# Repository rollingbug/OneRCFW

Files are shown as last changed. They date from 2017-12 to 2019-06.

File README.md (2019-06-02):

# OneRCFW
An Arduino/AVR based flight controller for RC fixed wing.  

    - 5 input channels (Throttle, Ailerons, Elevator, Rudder, flight mode)  
    - 4 output channels (0.5 us resolution PWM/PPM signal generator).  
    - Airplane NED attitude tracking function (with 6 DOF sensor, 200 Hz attitude update rate).
    - Airplane auto level (roll and pitch) control function.  
    - Airplane heading lock control function.  
    - Airplane flight mode control function (manual mode, auto level mode and GPS mode).  
    - Airplane GPS return to home function (unstabled, still need to do more test!)
    - RC output mixer function (for normal airplane, delta wing and V tail).  
    - 6 DOF sensor calibration function.  
    - Radio control stick position calibration function.    
    - Airplane failsafe function.  
    - Airplane configuration save/reload/reset function.  
    - Airplane runtime status monitoring function.  

PCB picture  

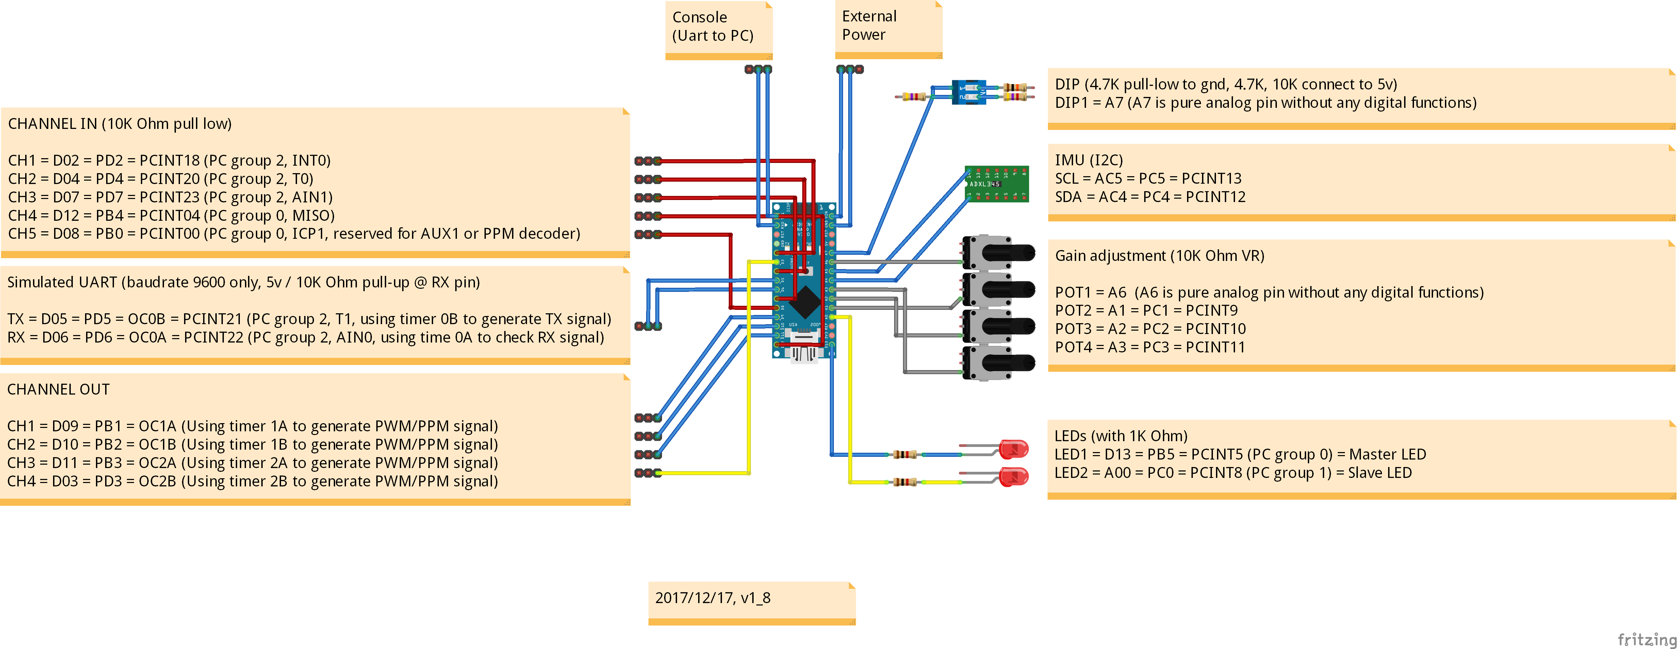
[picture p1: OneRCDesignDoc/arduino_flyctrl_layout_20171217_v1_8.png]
Pin assignment picture


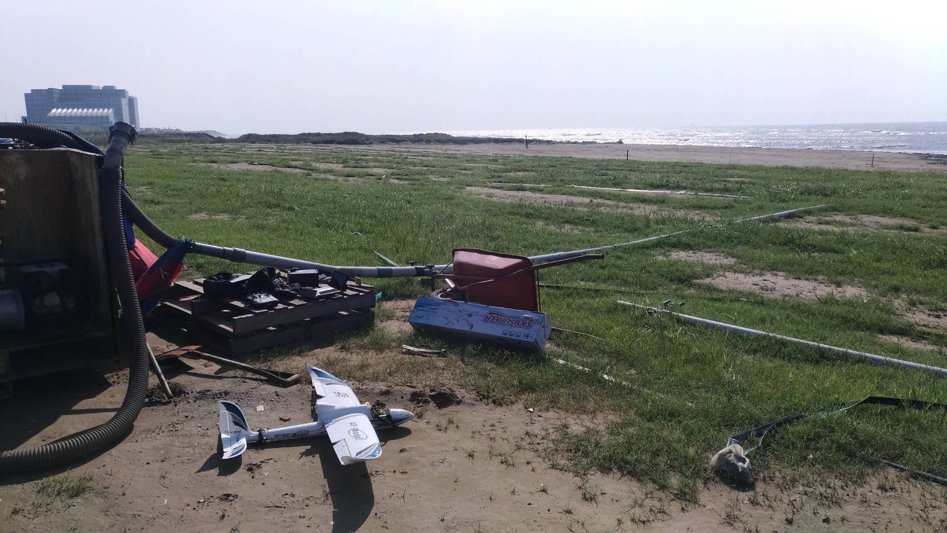
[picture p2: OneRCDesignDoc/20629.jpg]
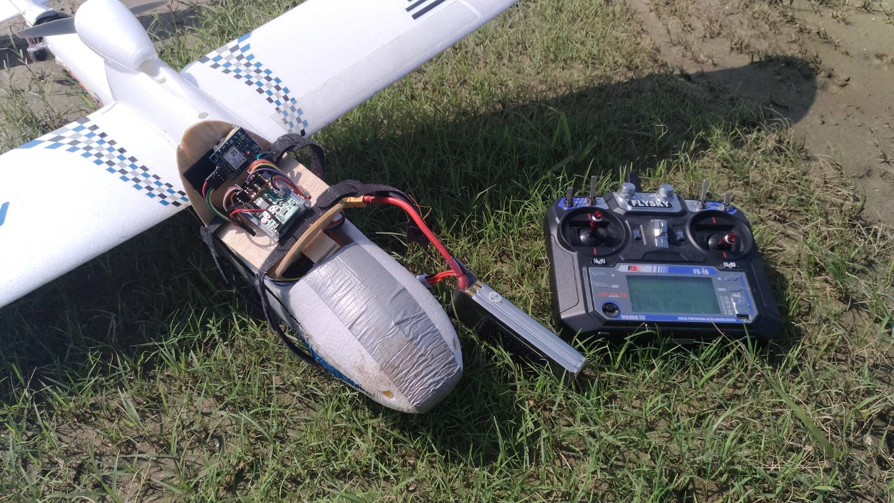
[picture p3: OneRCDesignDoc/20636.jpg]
  <br/><br/><br/>

Details:
---------------------
Flight controller source code: [OneRCFW](https://github.com/rollingbug/OneRCFW/tree/master/OneRCFW)  
Flight controller schematic and PCB layout: [OneRCSchematic_v1](https://github.com/rollingbug/OneRCFW/tree/master/OneRCSchematic/OneRCSchematic_v1)  
Flight controller test video: [20171029 FC test in very windy (12.5m/s) day.](https://www.youtube.com/watch?v=OjTpQ1Ft-OE)  
GUI monitoring tool: [OneRCGUI](https://github.com/rollingbug/OneRCFW/tree/master/OneRCGUI)  
Design documents: [OneRCDesignDoc](https://github.com/rollingbug/OneRCFW/tree/master/OneRCDesignDoc)   

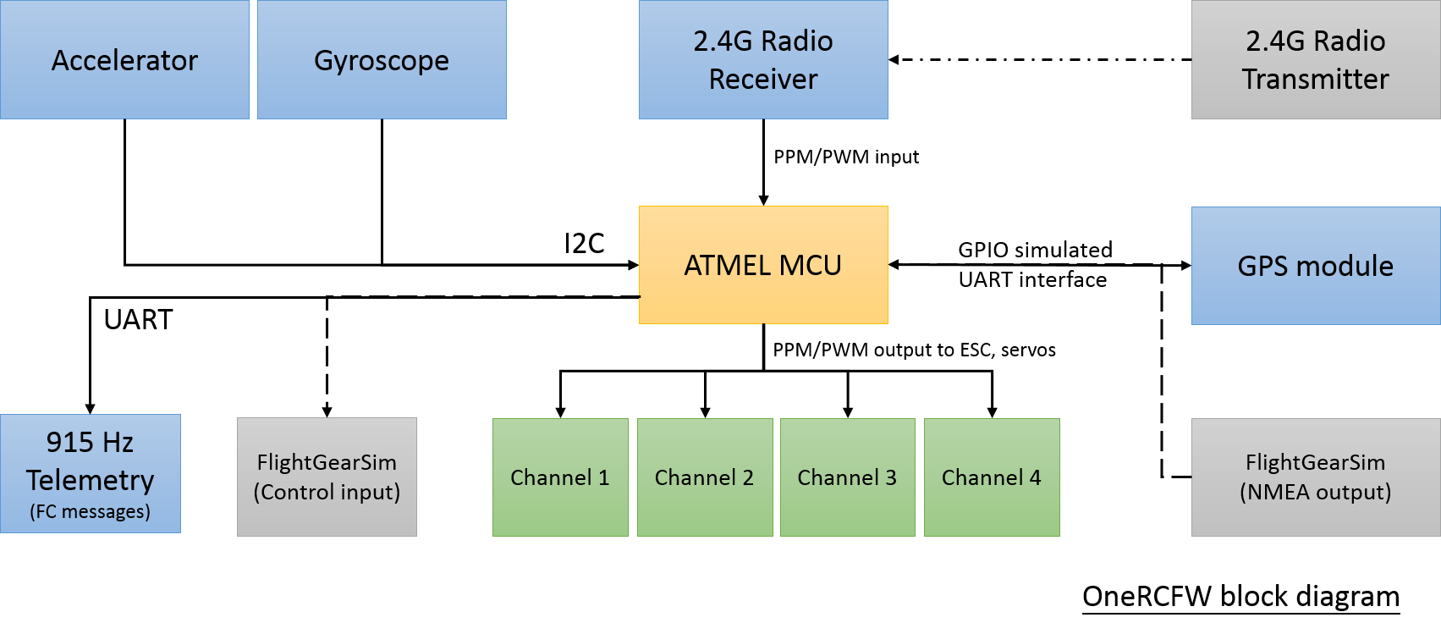
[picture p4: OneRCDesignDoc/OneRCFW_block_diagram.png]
FC block diagram


Build and Installation:
---------------------
1. Prepare Arduino 1.6.9 IDE.
2. Click the **OneRCAirplane.ino** to launch Arduino IDE. 
3. Change board type setting to "Arduino Nano" or "Pro Mini" and correct UART port setting.
4. Build and upload the firmware to Arduino or customized PCB.
5. Connect the Radio receiver to flight controller.
6. Check the channel output signal and the status of on board LEDs.<br/><br/><br/>

For Simulation mode:
---------------------
1. Download and instll FlightGear, and copy the protocol and configuration file to speicfic folder.
    - Copy [MAVLink.xml](https://github.com/rollingbug/OneRCFW/tree/master/OneRCFlightGearConf/MAVLink.xml) to FlightGear\data\Protocol\
    - Copy [.fgfsrc](https://github.com/rollingbug/OneRCFW/tree/master/OneRCFlightGearConf/.fgfsrc) to C:\Documents and Settings\{User name}\
2. Modify the #define IMU_SENSOR_MPU6050 in imu_ctrl.h, change to #define IMU_SENSOR_FG_SIM.
3. Rebuild and upload the firmware to Arduino.
4. Modify the COM port setting in both the [MP_fdm_nmea.py](https://github.com/rollingbug/OneRCFW/tree/master/OneRCGUI/MP_fdm_nmea.py) and [MP_fdm_sim.py](https://github.com/rollingbug/OneRCFW/tree/master/OneRCGUI/MP_fdm_sim.py), and lanuch these 2 files.
5. Lanuch fgfs.exe and enjoy the flight in simulator.

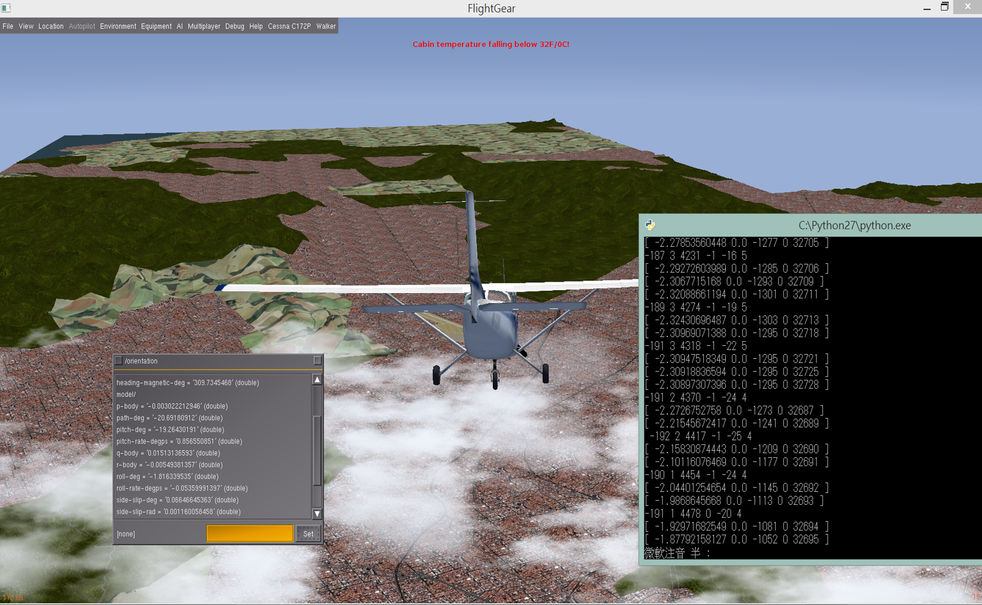
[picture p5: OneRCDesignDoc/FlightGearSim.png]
OneRC_FG_Simulator


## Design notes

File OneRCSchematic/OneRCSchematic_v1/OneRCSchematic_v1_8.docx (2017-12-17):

2017/08/19, v1.8

Part | Value | Package | Description | MF | MPN | BOM
C1 | 10uF | EIA3216 | CAP-00811 | AVX | TAJA106K010RNJ (10V, 10%) | 001
C2 | 10uF | EIA3216 | CAP-00811 | AVX | TAJA106K010RNJ (10V, 10%) | 001
C3 | 10nF (0402) | 0402-CAP | Capacitor | MuRata | GRM155R71H103KA88D (50v, X7R 10%) | 002
C4 | 1.0uF (0402) | 0402-CAP | Capacitor | YAGEO | CC0402KRX5R5BB105 (6.3v) | 003
C5 | 1.0uF (0402) | 0402-CAP | Capacitor | YAGEO | CC0402KRX5R5BB105 (6.3v) | 003
C6 | 0.1uF (0402) | 0402-CAP | Capacitor | MuRata | GRM155R71H104KE14D(50v, X7R 10%) | 004
C7 | 0.1uF (0402) | 0402-CAP | Capacitor | MuRata | GRM155R71H104KE14D(50v, X7R 10%) | 004
C8 | 0.1uF (0402) | 0402-CAP | Capacitor | MuRata | GRM155R71H104KE14D(50v, X7R 10%) | 004
C9 | 0.1uF (0402) | 0402-CAP | Capacitor | MuRata | GRM155R71H104KE14D(50v, X7R 10%) | 004
C10 | 10nF (0402) | 0402-CAP | Capacitor | MuRata | GRM155R71H103KA88D (50v, X7R 10%) | 002
C11 | 2.2nF (0402) | 0402-CAP | Capacitor | YAGEO | CC0402KRX7R9BB222, 2.2nF50V±10% | 005
C12 | 0.1uF (0402) | 0402-CAP | Capacitor | MuRata | GRM155R71H104KE14D(50v, X7R 10%) | 004
D1 | WHITE | 0402-LED | | CHIPLED | GTG1005SYGC | 200
D2 | RED | LED-0603 | Assorted Red LEDs | CHIPLED | GTG1608SURC | 201
D3 | BLUE | LED-0603 | Blue LEDs for production use | CHIPLED | GTG1608UBC | 202
J1 | BAT | 1X03 | Header 3 | UNKNOWN | UNKNOWN | 800
J2 | IN1 | 1X03 | Header 3 | UNKNOWN | UNKNOWN | 800
J3 | IN2 | 1X03 | Header 3 | UNKNOWN | UNKNOWN | 800
J4 | IN3 | 1X03 | Header 3 | UNKNOWN | UNKNOWN | 800
J5 | IN4 | 1X03 | Header 3 | UNKNOWN | UNKNOWN | 800
J6 | IN5 | 1X03 | Header 3 | UNKNOWN | UNKNOWN | 800
J7 | OUT1 | 1X03 | Header 3 | UNKNOWN | UNKNOWN | 800
J8 | OUT2 | 1X03 | Header 3 | UNKNOWN | UNKNOWN | 800
J9 | OUT3 | 1X03 | Header 3 | UNKNOWN | UNKNOWN | 800
J10 | OUT4 | 1X03 | Header 3 | UNKNOWN | UNKNOWN | 800
PH1 | PH1X3-05 | PH005-1-3 | | UNKNOWN | UNKNOWN | 801
PH2 | PH1X7-05 | PH005-1-7 | | UNKNOWN | UNKNOWN | 801
PH3 | PH1X4-05 | PH005-1-4 | | UNKNOWN | UNKNOWN | 801
R1 | 10K (0402) | 0402-RES | Resistor | YAGEO | RC0402FR-0710K | 100
R2 | 10K (0402) | 0402-RES | Resistor | YAGEO | RC0402FR-0710K | 100
R3 | 10K (0402) | 0402-RES | Resistor | YAGEO | RC0402FR-0710K | 100
R4 | 10K (0402) | 0402-RES | Resistor | YAGEO | RC0402FR-0710K | 100
R5 | 10K (0402) | 0402-RES | Resistor | YAGEO | RC0402FR-0710K | 100
R6 | 1K (0402) | 0402-RES | Resistor | YAGEO | RC0402FR-071K | 100
R7 | 10K (0402) | 0402-RES | Resistor | YAGEO | RC0402FR-0710K | 100
R8 | POT1 | RTRIM3202 | Trimm resistor | Panasonic | EVM3ESX50B14 | 101
R9 | POT2 | RTRIM3202 | Trimm resistor | Panasonic | EVM3ESX50B14 | 101
R10 | POT3 | RTRIM3202 | Trimm resistor | Panasonic | EVM3ESX50B14 | 101
R11 | 10K (0402) | 0402-RES | Resistor | YAGEO | RC0402FR-0710K | 100
R12 | POT4 | RTRIM3202 | Trimm resistor | Panasonic | EVM3ESX50B14 | 101
R13 | 4K7 (0402) | 0402-RES | Resistor | YAGEO | RC0402FR-074K7 | 102
R14 | 1K (0402) | 0402-RES | Resistor | YAGEO | RC0402FR-071K | 103
R15 | 4K7 (0402) | 0402-RES | Resistor | YAGEO | RC0402FR-074K7 | 102
R16 | 1K (0402) | 0402-RES | Resistor | YAGEO | RC0402FR-071K | 103
R17 | 10K (0402) | 0402-RES | Resistor | YAGEO | RC0402FR-0710K | 100
R18 | 10K (0402) | 0402-RES | Resistor | YAGEO | RC0402FR-0710K | 100
R19 | 10K (0402) | 0402-RES | Resistor | YAGEO | RC0402FR-0710K | 100
R20 | 10K (0402) | 0402-RES | Resistor | YAGEO | RC0402FR-0710K | 100
R21 | 10K (0402) | 0402-RES | Resistor | YAGEO | RC0402FR-0710K | 100
R22 | 10K (0402) | 0402-RES | Resistor | YAGEO | RC0402FR-0710K | 100
R23 | 10K (0402) | 0402-RES | Resistor | YAGEO | RC0402FR-0710K | 100
SW1 | SW1 | DIPSWITCH-02-50MIL | DIP SWITCH | Kingtek | DSHP02TSGET (1.27mm, 2P) | 700
T1 | 2N7002PW | SOT323 | N-channel TrenchMOS FET | ROHM | 2SK3018T106 | 903
T2 | 2N7002PW | SOT323 | N-channel TrenchMOS FET | ROHM | 2SK3018T106 | 903
U1 | RT9167 | SOT23-5 | MIC5205 150mA vreg | Richteck | RT9167A-33PB (3.3v, 500mA) | 900
U2 | MPU-6050 | QFN.24.4X4 | | InvenSense | MPU-6050 | 901
U3 | ATMEGA328P_TQFP | TQFP32-08 | | Atmel | ATMEGA328P_TQFP | 902
X1 | 53047-06 | 53047-06 | CONNECTOR | MOLEX | 53047-0610-C | 802
X2 | ICSP | PHB_1MM27_2X03_SNT | Pin Header Box-Type, 1.27mm/0.5/50mil Pitch | Connfly | DS1031-06-2*50P8BV等長 | 803
X3 | 53047-04 | 53047-04 | CONNECTOR | MOLEX | 53047-0410 | 804
Y1 | 16MHZ | RESONATOR-SMD | Resonator | MuRata | CSTCE16M0V53-R0 | 600

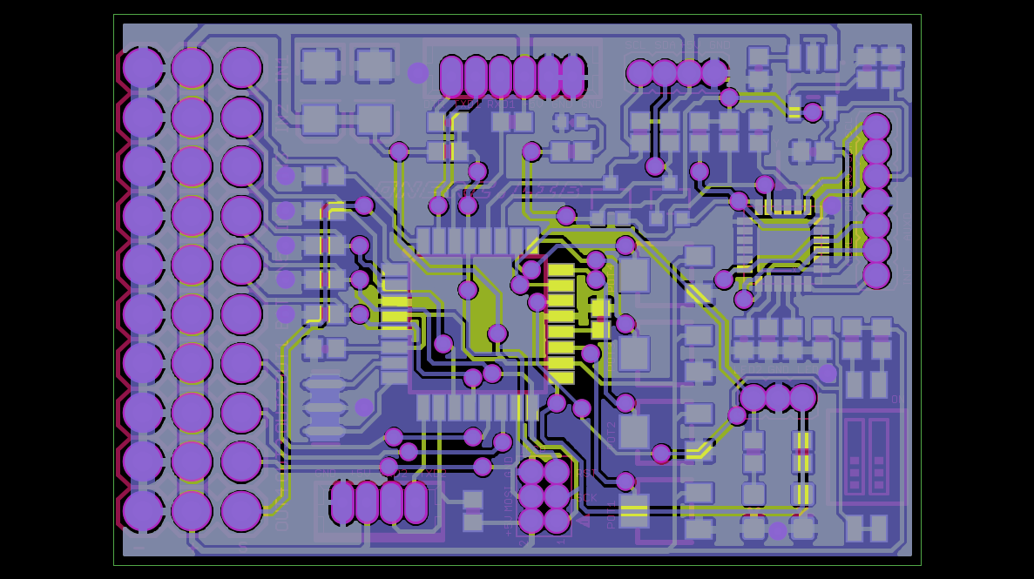
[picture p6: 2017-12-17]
OneRCSchematic/OneRCSchematic_v1/OneRCSchematic_v1_8.png

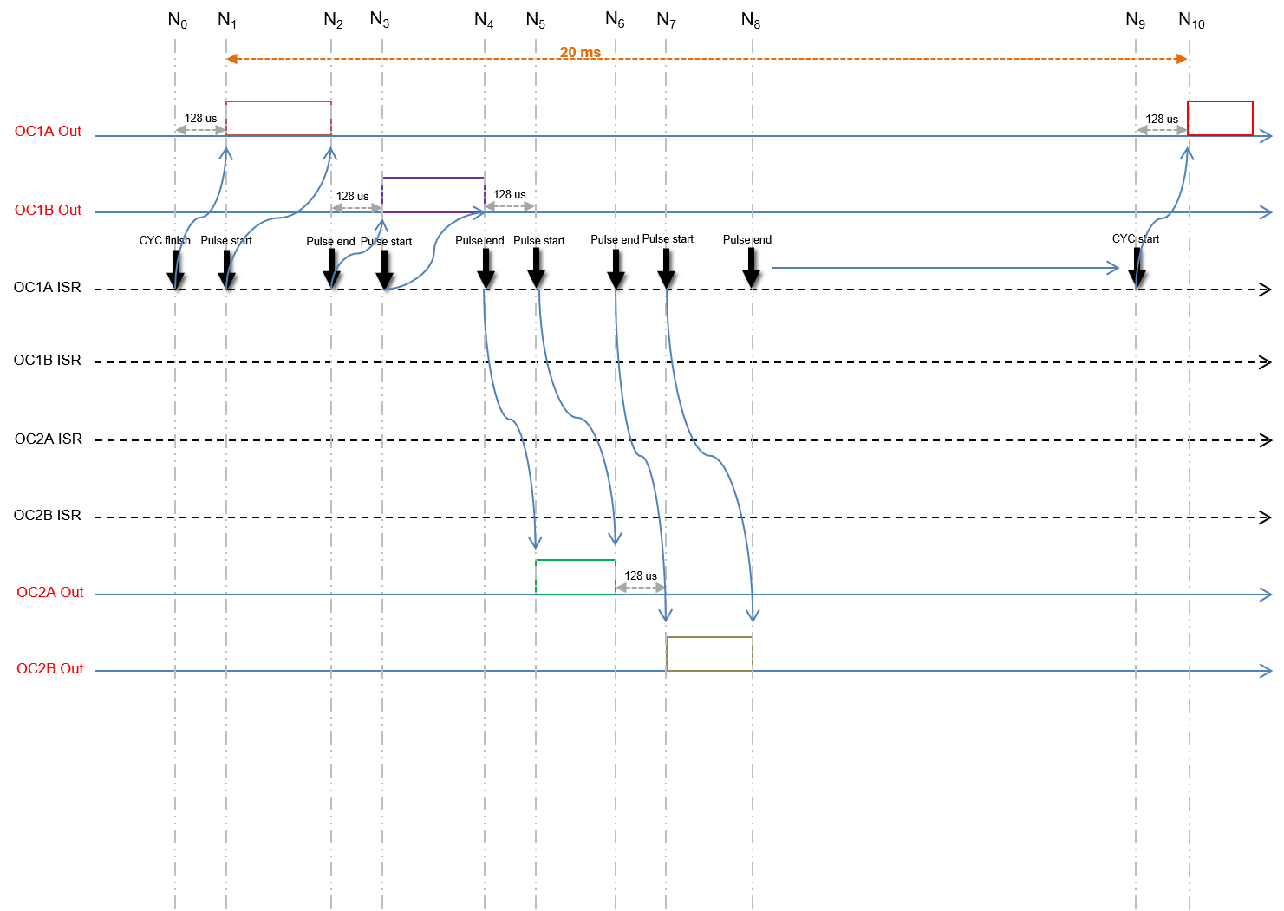
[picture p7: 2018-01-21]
OneRCDesignDoc/PWM_PPM_generator.png

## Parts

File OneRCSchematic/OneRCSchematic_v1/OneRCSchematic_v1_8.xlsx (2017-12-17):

Part | Value | Device | Package | Description | MF | MPN | BOM | NOTE | Ready | Price | OC_FARNELL | OC_NEWARK | PROD_ID | VALUE
C1 | 10uF | 10UF-16V-10%(TANT) | EIA3216 | CAP-00811 | AVX | TAJA106K010RNJ (10V, 10%) | 001 |  | Y |  |  |  | CAP-00811 | 10uF
C2 | 10uF | 10UF-16V-10%(TANT) | EIA3216 | CAP-00811 | AVX | TAJA106K010RNJ (10V, 10%) | 001 |  | Y |  |  |  | CAP-00811 | 10uF
C3 | 10nF (0402) | CAP0402-CAP | 0402-CAP | Capacitor | MuRata | GRM155R71H103KA88D (50v, X7R 10%) | 002 |  | Y
C4 | 1.0uF (0402) | CAP0402-CAP | 0402-CAP | Capacitor | YAGEO | CC0402KRX5R5BB105 (6.3v) | 003 | 參考3.3v LDO, 下次改用0603增加容值範圍? 10v, 1.0uf以上 | Y
C5 | 1.0uF (0402) | CAP0402-CAP | 0402-CAP | Capacitor | YAGEO | CC0402KRX5R5BB105 (6.3v) | 003 | 參考3.3v LDO, 下次改用0603增加容值範圍? 10v, 1.0uf以上 | Y
C6 | 0.1uF (0402) | CAP0402-CAP | 0402-CAP | Capacitor | MuRata | GRM155R71H104KE14D(50v, X7R 10%) | 004 |  | Y
C7 | 0.1uF (0402) | CAP0402-CAP | 0402-CAP | Capacitor | MuRata | GRM155R71H104KE14D(50v, X7R 10%) | 004 |  | Y
C8 | 0.1uF (0402) | CAP0402-CAP | 0402-CAP | Capacitor | MuRata | GRM155R71H104KE14D(50v, X7R 10%) | 004 |  | Y
C9 | 0.1uF (0402) | CAP0402-CAP | 0402-CAP | Capacitor | MuRata | GRM155R71H104KE14D(50v, X7R 10%) | 004 |  | Y
C10 | 10nF (0402) | CAP0402-CAP | 0402-CAP | Capacitor | MuRata | GRM155R71H103KA88D (50v, X7R 10%) | 002 |  | Y
C11 | 2.2nF (0402) | CAP0402-CAP | 0402-CAP | Capacitor | YAGEO | CC0402KRX7R9BB222, 2.2nF50V±10% | 005 | MPU6050, require 50v | Y
C12 | 0.1uF (0402) | CAP0402-CAP | 0402-CAP | Capacitor | MuRata | GRM155R71H104KE14D(50v, X7R 10%) | 004 |  | Y
D1 | WHITE | LED-0402 | 0402-LED |  | CHIPLED | GTG1005SYGC | 200 | 改用藍綠色 | Y
D2 | RED | LED-RED0603 | LED-0603 | Assorted Red LEDs | CHIPLED | GTG1608SURC | 201 | 紅色 | Y |  |  |  | DIO-00819 | RED
D3 | BLUE | LED-BLUE0603 | LED-0603 | Blue LEDs for production use | CHIPLED | GTG1608UBC | 202 | 藍色 | Y |  |  |  | DIO-08575 | BLUE
J1 | BAT | M03PTH | 1X03 | Header 3 | UNKNOWN | UNKNOWN | 800 |  | Y
J2 | IN1 | M03PTH | 1X03 | Header 3 | UNKNOWN | UNKNOWN | 800 |  | Y
J3 | IN2 | M03PTH | 1X03 | Header 3 | UNKNOWN | UNKNOWN | 800 |  | Y
J4 | IN3 | M03PTH | 1X03 | Header 3 | UNKNOWN | UNKNOWN | 800 |  | Y
J5 | IN4 | M03PTH | 1X03 | Header 3 | UNKNOWN | UNKNOWN | 800 |  | Y
J6 | IN5 | M03PTH | 1X03 | Header 3 | UNKNOWN | UNKNOWN | 800 |  | Y
J7 | OUT1 | M03PTH | 1X03 | Header 3 | UNKNOWN | UNKNOWN | 800 |  | Y
J8 | OUT2 | M03PTH | 1X03 | Header 3 | UNKNOWN | UNKNOWN | 800 |  | Y
J9 | OUT3 | M03PTH | 1X03 | Header 3 | UNKNOWN | UNKNOWN | 800 |  | Y
J10 | OUT4 | M03PTH | 1X03 | Header 3 | UNKNOWN | UNKNOWN | 800 |  | Y
PH1 | PH1X3-05 | PH1X3-05 | PH005-1-3 |  | UNKNOWN | UNKNOWN | 801 |  | Y
PH2 | PH1X7-05 | PH1X7-05 | PH005-1-7 |  | UNKNOWN | UNKNOWN | 801 |  | Y
PH3 | PH1X4-05 | PH1X4-05 | PH005-1-4 |  | UNKNOWN | UNKNOWN | 801 |  | Y
R1 | 10K (0402) | RESISTOR0402 | 0402-RES | Resistor | YAGEO | RC0402FR-0710K | 100 |  | Y
R2 | 10K (0402) | RESISTOR0402 | 0402-RES | Resistor | YAGEO | RC0402FR-0710K | 100 |  | Y
R3 | 10K (0402) | RESISTOR0402 | 0402-RES | Resistor | YAGEO | RC0402FR-0710K | 100 |  | Y
R4 | 10K (0402) | RESISTOR0402 | 0402-RES | Resistor | YAGEO | RC0402FR-0710K | 100 |  | Y
R5 | 10K (0402) | RESISTOR0402 | 0402-RES | Resistor | YAGEO | RC0402FR-0710K | 100 |  | Y
R6 | 1K (0402) | RESISTOR0402 | 0402-RES | Resistor | YAGEO | RC0402FR-071K | 100 |  | Y
R7 | 10K (0402) | RESISTOR0402 | 0402-RES | Resistor | YAGEO | RC0402FR-0710K | 100 |  | Y
R8 | POT1 | R-TRIMM3202 | RTRIM3202 | Trimm resistor | Panasonic | EVM3ESX50B14 | 101 |  | Y
R9 | POT2 | R-TRIMM3202 | RTRIM3202 | Trimm resistor | Panasonic | EVM3ESX50B14 | 101 |  | Y
R10 | POT3 | R-TRIMM3202 | RTRIM3202 | Trimm resistor | Panasonic | EVM3ESX50B14 | 101 |  | Y
R11 | 10K (0402) | RESISTOR0402 | 0402-RES | Resistor | YAGEO | RC0402FR-0710K | 100 |  | Y
R12 | POT4 | R-TRIMM3202 | RTRIM3202 | Trimm resistor | Panasonic | EVM3ESX50B14 | 101 |  | Y
R13 | 4K7 (0402) | RESISTOR0402 | 0402-RES | Resistor | YAGEO | RC0402FR-074K7 | 102 |  | Y
R14 | 1K (0402) | RESISTOR0402 | 0402-RES | Resistor | YAGEO | RC0402FR-071K | 103 |  | Y
R15 | 4K7 (0402) | RESISTOR0402 | 0402-RES | Resistor | YAGEO | RC0402FR-074K7 | 102 |  | Y
R16 | 1K (0402) | RESISTOR0402 | 0402-RES | Resistor | YAGEO | RC0402FR-071K | 103 |  | Y
R17 | 10K (0402) | RESISTOR0402 | 0402-RES | Resistor | YAGEO | RC0402FR-0710K | 100 |  | Y
R18 | 10K (0402) | RESISTOR0402 | 0402-RES | Resistor | YAGEO | RC0402FR-0710K | 100 |  | Y
R19 | 10K (0402) | RESISTOR0402 | 0402-RES | Resistor | YAGEO | RC0402FR-0710K | 100 |  | Y
R20 | 10K (0402) | RESISTOR0402 | 0402-RES | Resistor | YAGEO | RC0402FR-0710K | 100 |  | Y
R21 | 10K (0402) | RESISTOR0402 | 0402-RES | Resistor | YAGEO | RC0402FR-0710K | 100 |  | Y
R22 | 10K (0402) | RESISTOR0402 | 0402-RES | Resistor | YAGEO | RC0402FR-0710K | 100 |  | Y
R23 | 10K (0402) | RESISTOR0402 | 0402-RES | Resistor | YAGEO | RC0402FR-0710K | 100 |  | Y
SW1 | SW1 | SW_DIP-2-SMT-HALFSIZE | DIPSWITCH-02-50MIL | DIP SWITCH | Kingtek | DSHP02TSGET (1.27mm, 2P) | 700 |  | Y
T1 | 2N7002PW | 2N7002PW | SOT323 | N-channel TrenchMOS FET | ROHM | 2SK3018T106 | 903 |  | Y
T2 | 2N7002PW | 2N7002PW | SOT323 | N-channel TrenchMOS FET | ROHM | 2SK3018T106 | 903 |  | Y
U1 | RT9167 | MIC52053.3V | SOT23-5 | MIC5205 150mA vreg | Richteck | RT9167A-33PB (3.3v, 500mA) | 900 |  | Y |  |  |  | VREG-00822
U2 | MPU-6050 | MPU-6050 | QFN.24.4X4 |  | InvenSense | MPU-6050 | 901 |  | Y
U3 | ATMEGA328P_TQFP | ATMEGA328P_TQFP | TQFP32-08 |  | Atmel | ATMEGA328P_TQFP | 902 |  | N |  |  |  | IC-09069 | ATMEGA328P_TQFP
X1 | 53047-06 | 53047-06 | 53047-06 | CONNECTOR | MOLEX | 53047-0610-C | 802 |  | Y |  | 9733078 | 03M2965
X2 | ICSP | PHB_1MM27_2X03_SNT | PHB_1MM27_2X03_SNT | Pin Header Box-Type, 1.27mm/0.5/50mil Pitch | Connfly | DS1031-06-2*50P8BV等長 | 803 |  | Y
X3 | 53047-04 | 53047-04 | 53047-04 | CONNECTOR | MOLEX | 53047-0410 | 804 |  | Y |  | 9733060 | 38C9900
Y1 | 16MHZ | RESONATOR16MHZ | RESONATOR-SMD | Resonator | MuRata | CSTCE16M0V53-R0 | 600 |  | Y |  |  |  | XTAL-08900 | 16MHZ

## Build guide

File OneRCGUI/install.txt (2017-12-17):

python -m pip install numpy
python -m pip install matplotlib
python -m pip install PyOpenGL
python -m pip install pysdl2

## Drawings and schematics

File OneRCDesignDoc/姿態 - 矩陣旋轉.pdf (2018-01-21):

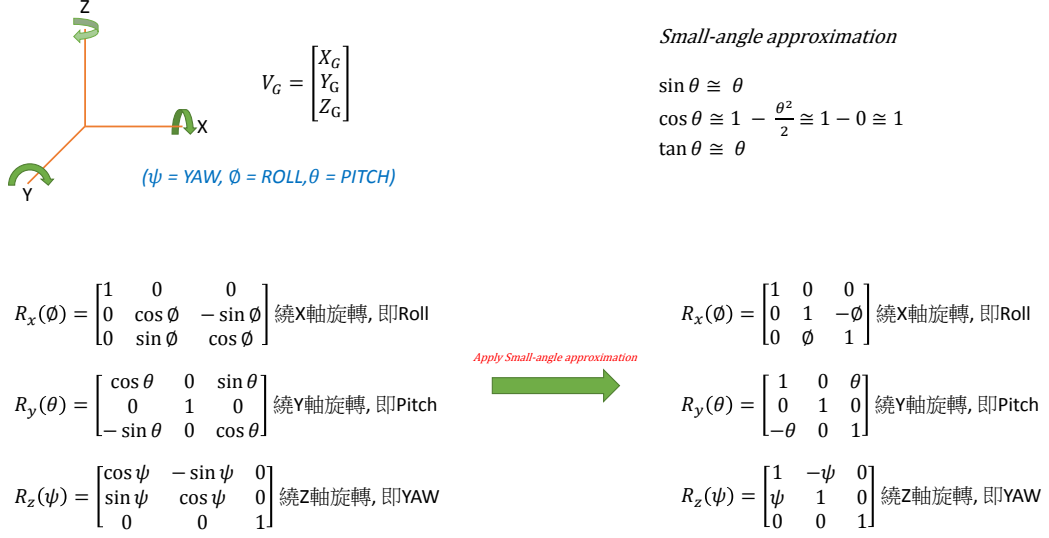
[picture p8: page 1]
0 cos ∅ − sin ∅; 0 sin ∅; cos ∅; 繞X軸旋轉, 即Roll; cos θ; 0 sin θ; − sin θ 0 cos θ; 繞Y軸旋轉, 即Pitch; cos ψ − sin ψ 0; sin ψ; cos ψ; 繞Z軸旋轉, 即YAW; sin θ ≅ θ; cos θ ≅ 1 −; tan θ ≅ θ

Small-angle approximation

(ψ = YAW, ∅ = ROLL,θ = PITCH)

Apply Small-angle approximation

VG =

XG
YG
Vnew_G = Rx ∅ ∙ Ry θ ∙ Rz ψ ∙ VG

ZG

Vnew_G =

1 | 0 | 0
0 cos ∅ − sin ∅
0 sin ∅ cos ∅

∙

cos θ | 0 sin θ
0 | 1 | 0
− sin θ 0 cos θ

∙

cos ψ − sin ψ 0
sin ψ | cos ψ | 0
0 | 0 | 1

∙

XG
YG
ZG

Vnew_G ≅

1 0 0
0 1 −∅
0 ∅ 1

∙

1 | 0 θ
0 | 1 0
−θ 0 1

∙

1 −ψ 0
ψ | 1 | 0
0 | 0 | 1

∙

XG
YG
ZG

Vnew_G ≅

1 | 0 | θ
∅θ 1 −∅
−θ ∅ 1

∙

1 −ψ 0
ψ | 1 | 0
0 | 0 | 1

∙

XG
YG
ZG

Vnew_G ≅

1 | −ψ | θ
∅θ + ψ | −∅θψ + 1 −∅
−θ + ∅ψ | θψ + ∅ | 1

∙

XG
YG
ZG

Vnew_G ≅

1 | −ψ | θ
θ∅ + ψ | −∅θψ + 1 −∅
−θ + ∅ψ | θψ + ∅ | 1

∙

XG
YG
ZG

Vnew_G ≅

1 | −ψ | θ
ψ | 1 | −∅
−θ | ∅ | 1

∙

XG
YG
ZG

≅

XG − ψYG + θZG
YG + ψXG − ∅ZG
ZG − θXG + ∅YG

Small-angle approximation

sin θ ≅ θ
cos θ ≅ 1 −

θ

2

2

≅ 1 − 0 ≅ 1
tan θ ≅ θ

∅θψ ≅ 0 ,
∅θ ≅ 0 ,
∅ψ ≅ 0 ,
θψ ≅ 0

int vector[3] = {0, 0, 1}; int x_g = vector[0];
int y_g = vector[1];
int z_g = vector[2];
int yaw = 1, pitch = 1, roll = 1;

/* Small-angle approximation matrix rotation */
vector[0] = vector[0] - yaw * y_g + pitch * z_g; | /* x_g_new */
vector[1] = vector[1] + yaw * x_g - roll * z_g; | /* y_g_new */
vector[2] = vector[2] - pitch * x_g + roll * y_g; /* z_g_new */

(ψ = YAW, ∅ = ROLL, θ = PITCH)

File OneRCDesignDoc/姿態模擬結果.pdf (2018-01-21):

## Accelerometer vibration

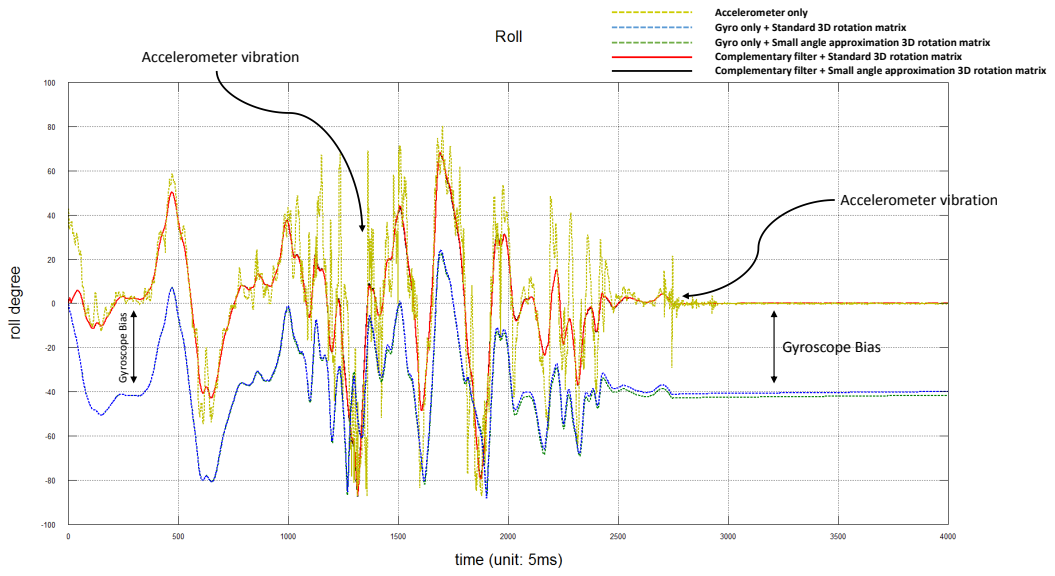
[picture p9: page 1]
Gyroscope Bias; Accelerometer vibration

Accelerometer only
Gyro only + Standard 3D rotation matrix
Gyro only + Small angle approximation 3D rotation matrix
Complementary filter + Standard 3D rotation matrix
Complementary filter + Small angle approximation 3D rotation matrix

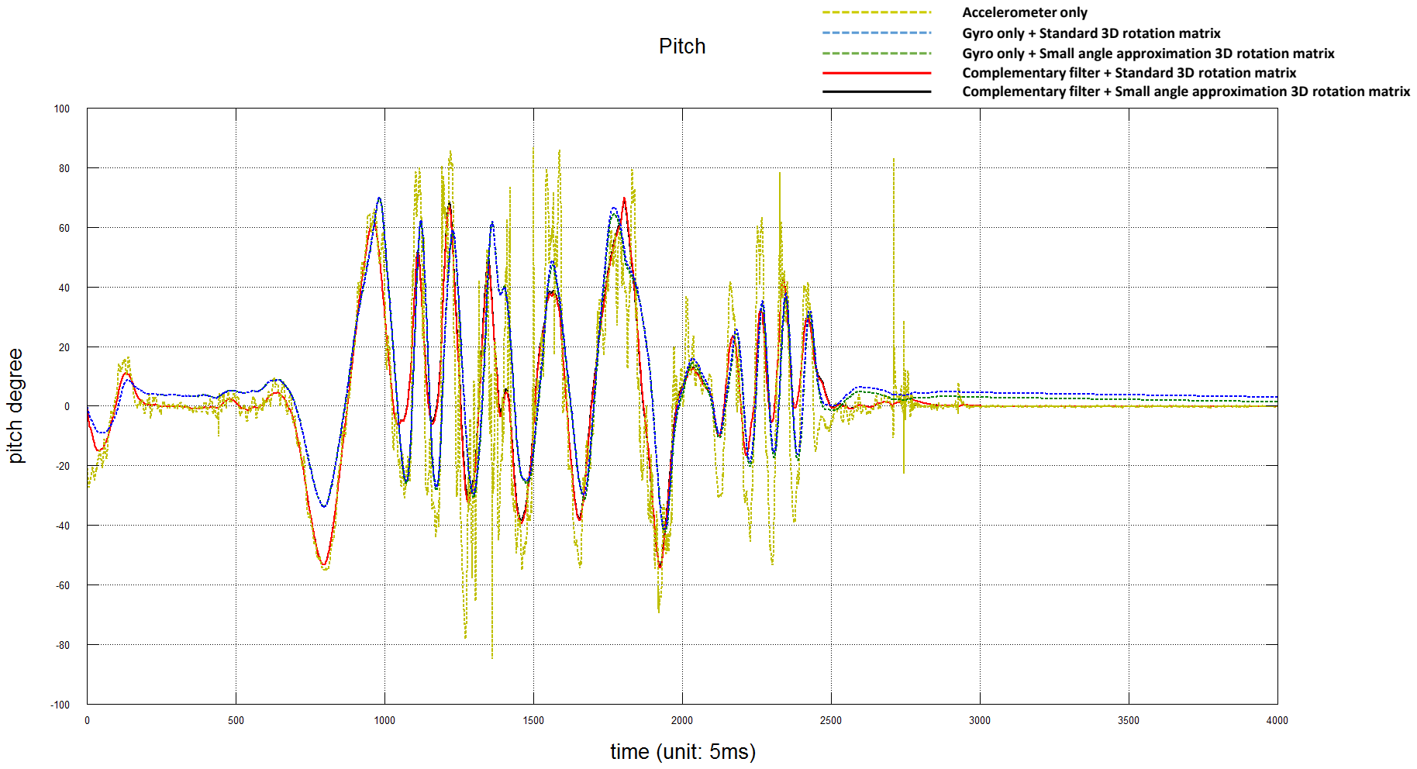
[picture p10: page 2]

Gyro only + Small angle approximation 3D rotation matrix

Gyro only + Standard 3D rotation matrix

Accelerometer only

Complementary filter + Standard 3D rotation matrix
Complementary filter + Small angle approximation 3D rotation matrix

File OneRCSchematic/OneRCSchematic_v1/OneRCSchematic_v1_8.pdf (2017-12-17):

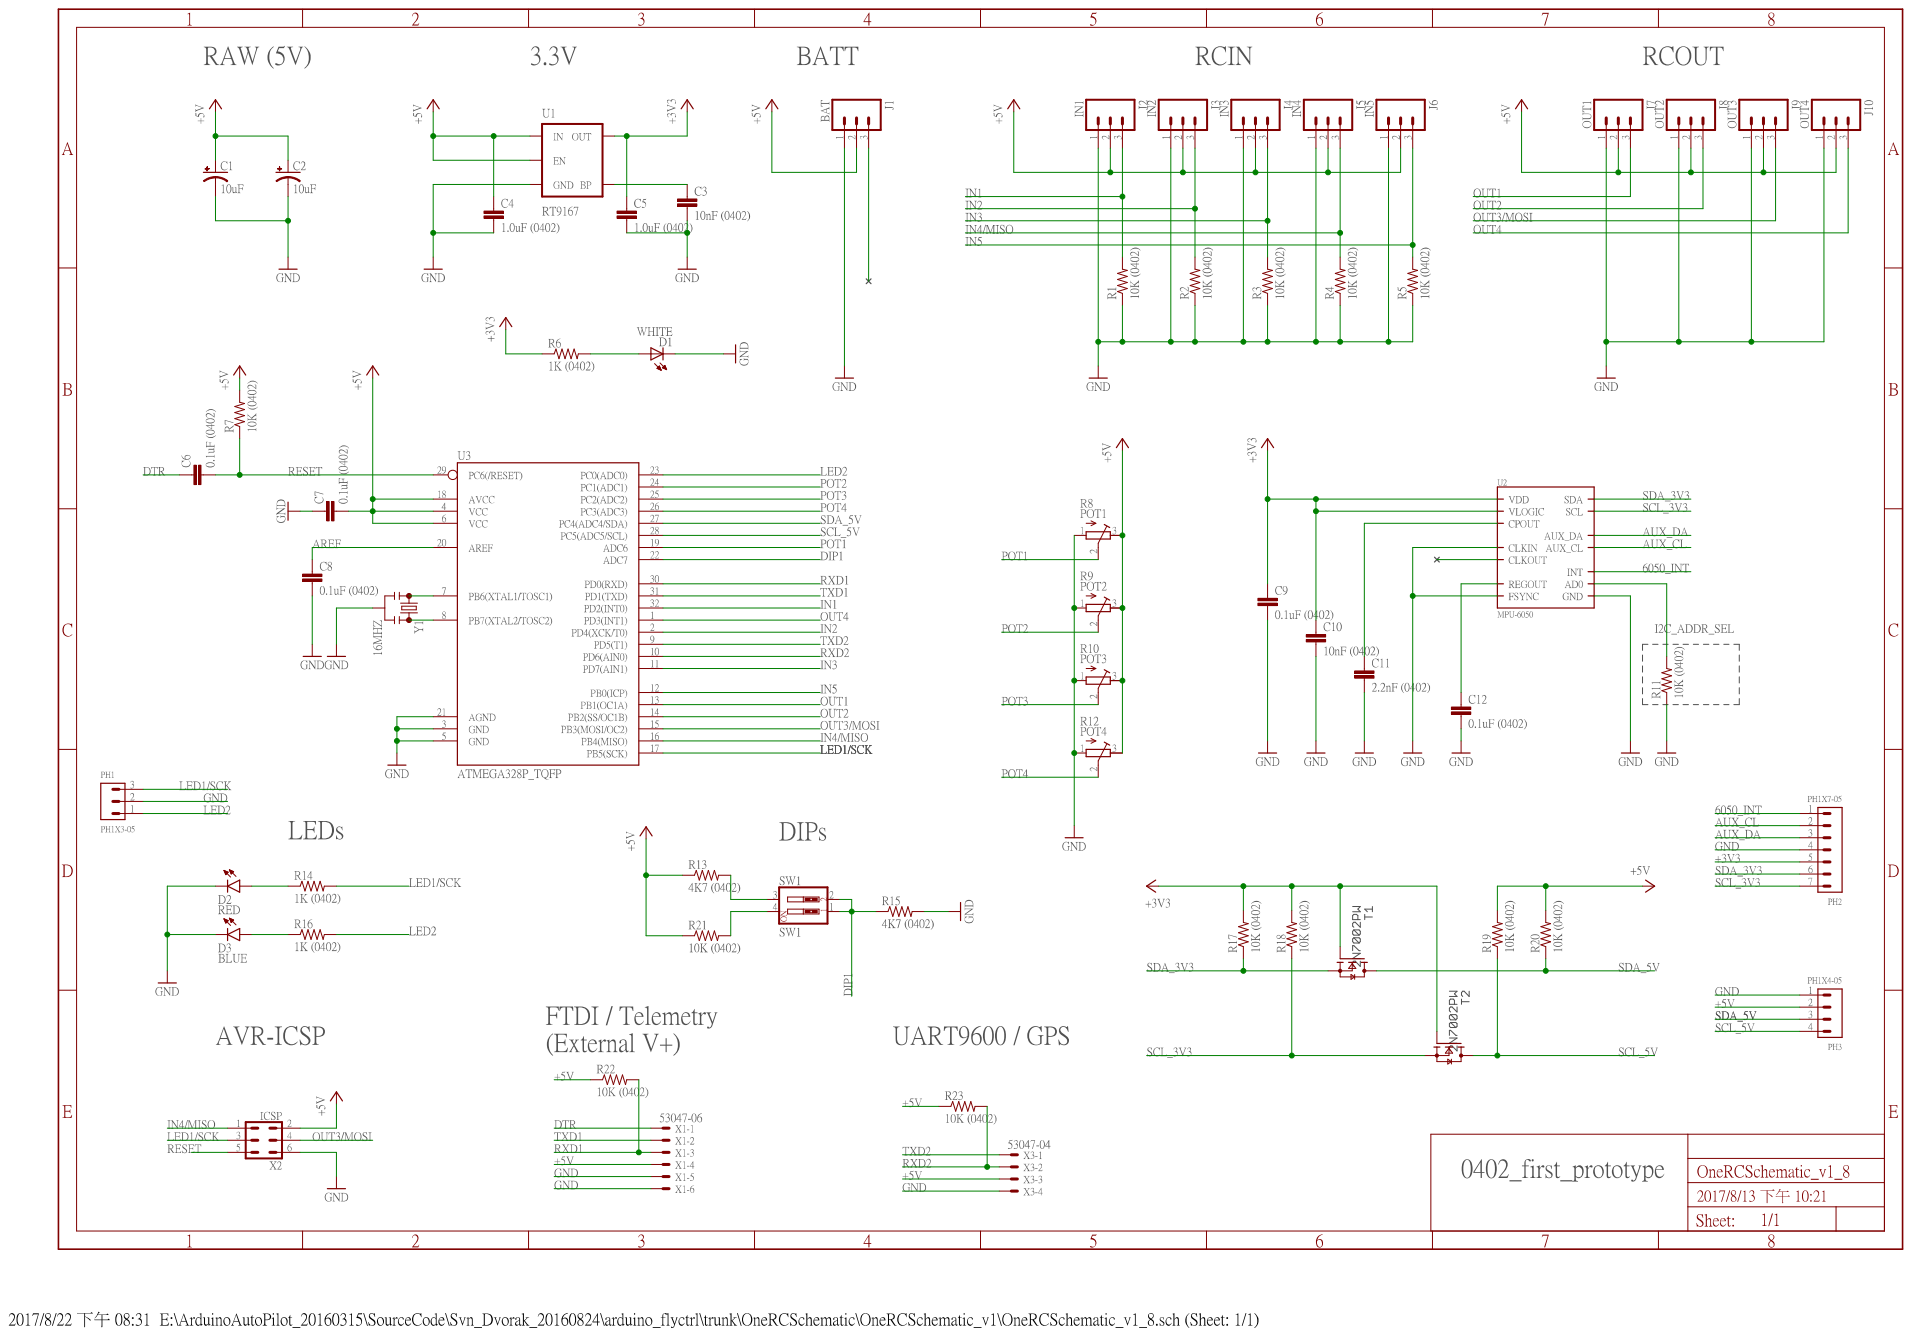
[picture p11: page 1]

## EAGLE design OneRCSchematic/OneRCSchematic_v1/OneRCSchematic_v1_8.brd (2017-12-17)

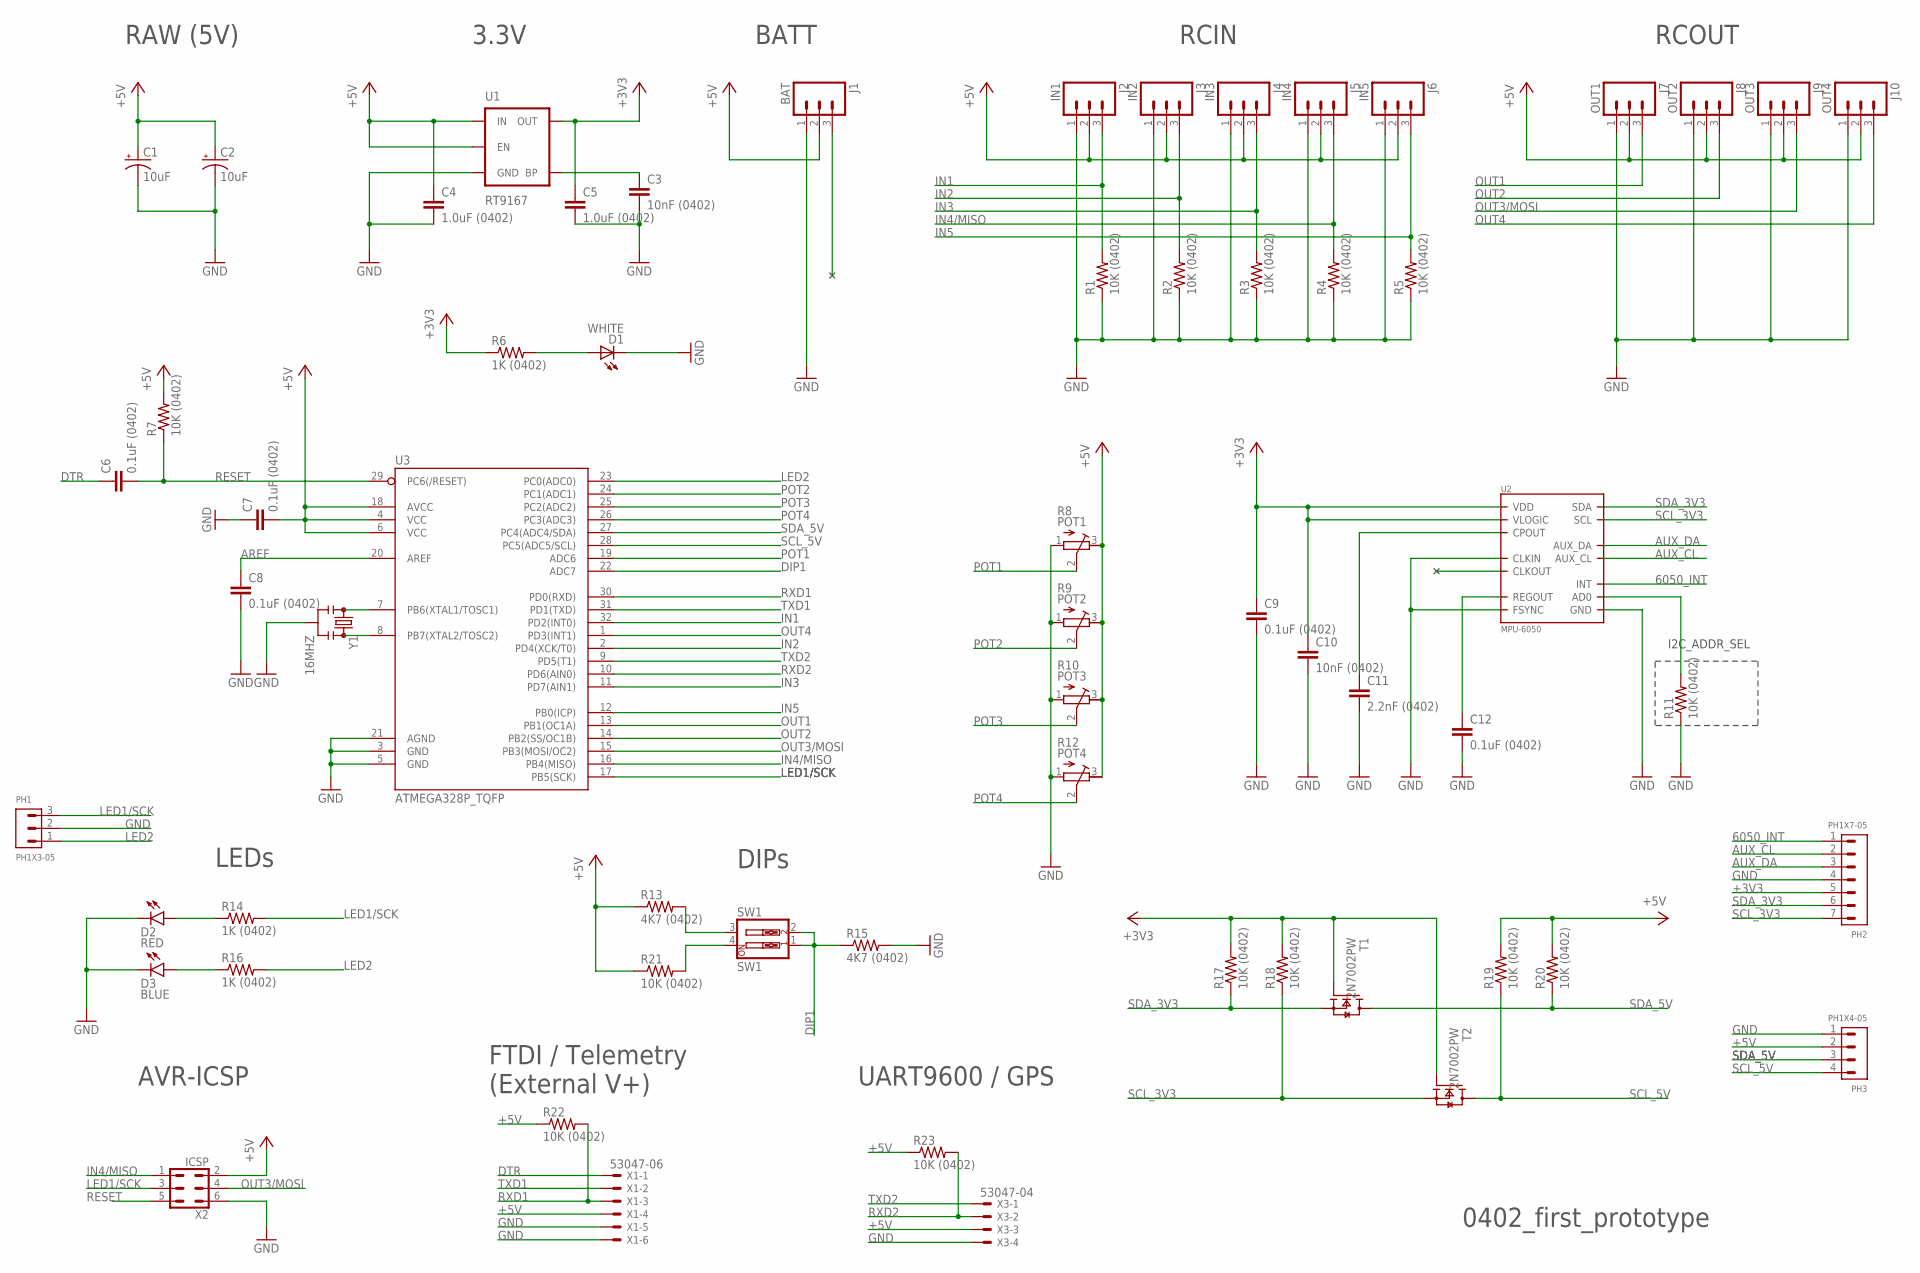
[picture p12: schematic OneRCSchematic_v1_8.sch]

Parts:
C1, C2: 10uF; EIA3216
C3, C10: 10nF (0402); 0402-CAP
C4, C5: 1.0uF (0402); 0402-CAP
C6, C7, C8, C9, C12: 0.1uF (0402); 0402-CAP
C11: 2.2nF (0402); 0402-CAP
D1: WHITE; 0402-LED
D2: RED; LED-0603
D3: BLUE; LED-0603
J1: BAT; 1X03
J2: IN1; 1X03
J3: IN2; 1X03
J4: IN3; 1X03
J5: IN4; 1X03
J6: IN5; 1X03
J7: OUT1; 1X03
J8: OUT2; 1X03
J9: OUT3; 1X03
J10: OUT4; 1X03
PH1: PH1X3-05; PH005-1-3
PH2: PH1X7-05; PH005-1-7
PH3: PH1X4-05; PH005-1-4
R1, R2, R3, R4, R5, R7, R11, R17, R18, R19, R20, R21, R22, R23: 10K (0402); 0402-RES
R6, R14, R16: 1K (0402); 0402-RES
R8: POT1; RTRIM3202
R9: POT2; RTRIM3202
R10: POT3; RTRIM3202
R12: POT4; RTRIM3202
R13, R15: 4K7 (0402); 0402-RES
SW1: SW1; DIPSWITCH-02-50MIL
T1, T2: 2N7002PW; SOT323
U1: RT9167; SOT23-5
U2: MPU-6050; QFN.24.4X4
U3: ATMEGA328P_TQFP; TQFP32-08
X1: 53047-06
X2: ICSP; PHB_1MM27_2X03_SNT
X3: 53047-04
Y1: 16MHZ; RESONATOR-SMD

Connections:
6050_INT: PH2.1, U2.12 (INT)
+3V3: C5.1, C9.1, C10.1, PH2.5, R6.1, R17.2, R18.2, T1.1 (G), T2.1 (G), U1.5 (OUT), U2.8 (VLOGIC), U2.13 (VDD)
+5V: C1.A (+), C2.A (+), C4.1, C7.2, J1.2, J2.2, J3.2, J4.2, J5.2, J6.2, J7.2, J8.2, J9.2, J10.2, PH3.2, R7.2, R8.3 (E), R9.3 (E), R10.3 (E), R12.3 (E), R13.1, R19.2, R20.2, R21.1, R22.1, R23.1, U1.1 (IN), U1.3 (EN), U3.4 (VCC), U3.6 (VCC), U3.18 (AVCC), X1.4, X2.2, X3.3
AREF: C8.1, U3.20 (AREF)
AUX_CL: PH2.2, U2.7 (AUX_CL)
AUX_DA: PH2.3, U2.6 (AUX_DA)
DIP1: R15.1, SW1.1, SW1.2, U3.22 (ADC7)
DTR: C6.1, X1.1
GND: C1.C (-), C2.C (-), C3.2, C4.2, C5.2, C7.1, C8.2, C9.2, C10.2, C11.2, C12.2, D1.C, D2.C, D3.C, J1.1, J2.1, J3.1, J4.1, J5.1, J6.1, J7.1, J8.1, J9.1, J10.1, PH1.2, PH2.4, PH3.1, R1.1, R2.1, R3.1, R4.1, R5.1, R8.1 (A), R9.1 (A), R10.1 (A), R11.1, R12.1 (A), R15.2, U1.2 (GND), U2.1 (CLKIN), U2.11 (FSYNC), U2.18 (GND), U3.3 (GND), U3.5 (GND), U3.21 (AGND), X1.5, X1.6, X2.6, X3.4, Y1.2
IN1: J2.3, R1.2, U3.32 (PD2(INT0))
IN2: J3.3, R2.2, U3.2 (PD4(XCK/T0))
IN3: J4.3, R3.2, U3.11 (PD7(AIN1))
IN4/MISO: J5.3, R4.2, U3.16 (PB4(MISO)), X2.1
IN5: J6.3, R5.2, U3.12 (PB0(ICP))
LED1/SCK: PH1.3, R14.2, U3.17 (PB5(SCK)), X2.3
LED2: PH1.1, R16.2, U3.23 (PC0(ADC0))
unnamed: D2.A, R14.1
unnamed: U3.7 (PB6(XTAL1/TOSC1)), Y1.1
unnamed: U3.8 (PB7(XTAL2/TOSC2)), Y1.3
unnamed: D3.A, R16.1
unnamed: D1.A, R6.2
unnamed: C3.1, U1.4 (BP)
unnamed: C11.1, U2.20 (CPOUT)
unnamed: C12.1, U2.10 (REGOUT)
unnamed: R13.2, SW1.3
unnamed: R21.2, SW1.4
unnamed: R11.2, U2.9 (AD0)
OUT1: J7.3, U3.13 (PB1(OC1A))
OUT2: J8.3, U3.14 (PB2(SS/OC1B))
OUT3/MOSI: J9.3, U3.15 (PB3(MOSI/OC2)), X2.4
OUT4: J10.3, U3.1 (PD3(INT1))
POT1: R8.2 (S), U3.19 (ADC6)
POT2: R9.2 (S), U3.24 (PC1(ADC1))
POT3: R10.2 (S), U3.25 (PC2(ADC2))
POT4: R12.2 (S), U3.26 (PC3(ADC3))
RESET: C6.2, R7.1, U3.29 (PC6(/RESET)), X2.5
RXD1: R22.2, U3.30 (PD0(RXD)), X1.3
RXD2: R23.2, U3.10 (PD6(AIN0)), X3.2
SCL_3V3: PH2.7, R18.1, T2.2 (S), U2.23 (SCL)
SCL_5V: PH3.4, R19.1, T2.3 (D), U3.28 (PC5(ADC5/SCL))
SDA_3V3: PH2.6, R17.1, T1.2 (S), U2.24 (SDA)
SDA_5V: PH3.3, R20.1, T1.3 (D), U3.27 (PC4(ADC4/SDA))
TXD1: U3.31 (PD1(TXD)), X1.2
TXD2: U3.9 (PD5(T1)), X3.1

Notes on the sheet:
LEDs
RCIN
RCOUT
3.3V
RAW (5V)
AVR-ICSP
FTDI / Telemetry (External V+)
UART9600 / GPS
DIPs
0402_first_prototype
I2C_ADDR_SEL
BATT

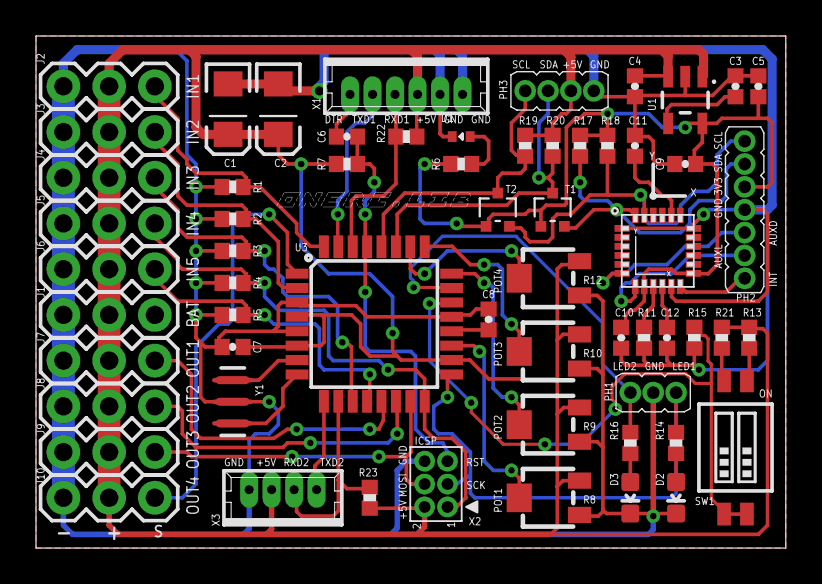
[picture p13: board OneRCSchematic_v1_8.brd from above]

Board: 2 copper layers, 41.7 x 28.4 mm, 62 parts (0 on the bottom side), 44 nets.

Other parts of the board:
U$2: ONE_RX_LOG_TINY_TOP

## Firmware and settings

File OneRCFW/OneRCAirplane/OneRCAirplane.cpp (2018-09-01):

/**
 *******************************************************************************
 *      ______  _   __  ______  ____     ______        ___    ______   ____
 *     / __  / / \ / / / ____/ / __ \   /  ___/       /  /   /_   _/  / __ \
 *    / /_/ / /   \ / / ____/ /  -- /  /  /__   __   /  /__  _/  /_  / __ <
 *   /_____/ /_/ \_/ /_____/ /__/ \_\ /_____/  /_/  /_____/ /_____/ /_____/
 *
 *     An amateur remote control software library. Use at your own risk.
 *
 * @file    OneRCAirplane.cpp
 * @brief
 *
 *          Abbreviations:
 *              DBG     - Debug             POT     - Potentiometer
 *
 * @author  Y.S.Kuo in Hsinchu
 *******************************************************************************
 */

#include <Arduino.h>
#include <string.h>
#include <OneRCLib.h>

#include "OneRCAirplane.h"


/*
 *******************************************************************************
 * Constant value definition
 *******************************************************************************
 */

#define AIRPLANE_KP_CH                  ADC_CH0
#define AIRPLANE_KI_CH                  ADC_CH1
#define AIRPLANE_KD_CH                  ADC_CH2

#define AIRPLANE_ROLL_SCALE_CH          ADC_CH0
#define AIRPLANE_PITCH_SCALE_CH         ADC_CH1
#define AIRPLANE_YAW_SCALE_CH           ADC_CH2
#define AIRPLANE_NAV_LOITER_CH          ADC_CH3
#define AIRPLANE_MODE_DIPS_CH           ADC_CH4

#define AIRPLANE_DIP_RC_CALI_ACTIVE     0
#define AIRPLANE_DIP_RC_CALI_START      1

#define AIRPLANE_RC_CALI_NONE           0
#define AIRPLANE_RC_CALI_NEUTRAL        1
#define AIRPLANE_RC_CALI_RANGE          2
#define AIRPLANE_RC_CALI_FAILSAFE       3
#define AIRPLANE_RC_CALI_FINISH         4

/* Potentiometers */
#define AIRPLANE_PID_POT_COMMON         1       /*
                                                 * Using 3 potentiometers to adjust
                                                 * KP, KI, KD of roll, pitch and yaw
                                                 * stabilizing control.
                                                 */
#define AIRPLANE_PID_POT_SCALE          2       /*
                                                 * Using 3 potentiometers to adjust
                                                 * the PID scale parameter of roll,
                                                 * pitch and yaw stabilizing control
                                                 * separately.
                                                 */


#define AIRPLANE_PID_POT_EN             true    /* To enable the Potentiometers on FC */

#define AIRPLANE_PID_POT_TYPE           AIRPLANE_PID_POT_SCALE

#define AIRPLANE_WPT_ARRIVE_RADIUS      10.0    /* Meters */

#define AIRPLANE_GET_LOITER_RADIUS()    ((ADC_Read(AIRPLANE_NAV_LOITER_CH) * 0.20)  \
                                         + AIRPLANE_WPT_ARRIVE_RADIUS)

#define AIRPLANE_WPT_NUM                5


/*
 *******************************************************************************
 * Data type definition
 *******************************************************************************
 */

typedef struct airplane_waypoint{
    bool is_actived;
    GPS_COORD_POINT wpt_coord;
}AIRPLANE_WAYPOINT;

typedef struct airplane_navigation{
    float loiter_radius;                    /* Loiter radius (meters) around home position */
    uint8_t current_wpt_idx;
    uint8_t total_wpt;
    AIRPLANE_WAYPOINT wpt[AIRPLANE_WPT_NUM];
}AIRPLANE_NAVIGATION;

typedef struct airplane_config{

    uint32_t config_ID;

    uint32_t config_date;

    AIRPLANE_TYPE model_type;

    bool is_imu_calibrated;
    int16_t accel_bias[IMU_AXES];
    int16_t gyro_bias[IMU_AXES];

    bool rc_in_is_reversed[RCIN_CH_TOTAL];
    uint16_t rc_in_neutral_ticks[RCIN_CH_TOTAL];
    uint16_t rc_in_max_ticks[RCIN_CH_TOTAL];
    uint16_t rc_in_min_ticks[RCIN_CH_TOTAL];
    uint16_t rc_in_failsafe_ticks[RCIN_CH_TOTAL];

    struct{
        float KP;
        float KI;
        float KD;
        float scale;
        float integral_max;
        float output_max;
    }pid_aile_cfg;

    struct{
        float KP;
        float KI;
        float KD;
        float scale;
        float integral_max;
        float output_max;
    }pid_elev_cfg;

    struct{
        float KP;
        float KI;
        float KD;
        float scale;
        float integral_max;
        float output_max;
    }pid_rudd_cfg;

    struct{
        float KP;
        float KI;
        float KD;
        float scale;
        float integral_max;
        float output_max;
    }pid_bank_turn_cfg;

    AIRPLANE_NAVIGATION navigation;

    uint16_t rom_crc16;

}AIRPLANE_CONFIG;

typedef struct airplane_status{
    AHRS_DATA ahrs_data;                    /* AHRS data */
    PID_DATA pid_aile_servo;                /* Ailerons servo PID data */
    PID_DATA pid_elev_servo;                /* Elevator servo PID data */
    PID_DATA pid_rudd_servo;                /* Rudder servo PID data */
    PID_DATA pid_band_turn;                 /* Bank turn PID data */

    struct{
        float roll_angle;
        float pitch_angle;
        float heading_angle;
    }setpoint;

    uint16_t rc_pulse_in[RCIN_CH_TOTAL];    /* RC pulse in */
    uint16_t rc_pulse_out[RCOUT_CH_TOTAL];  /* RC pulse out */

    struct{
        AIRPLANE_FLY_MODE fly_mode;

        uint8_t imu_fail_cnt;
        uint8_t ahrs_delay_cnt;
        uint8_t rcin_cyc_cnt;
        uint8_t rcout_cyc_cnt;

        uint16_t delta_ctrl_time;

        float mcu_vcc;

    }general;

    AIRPLANE_CRUISE_STATE current_cruise_state;

    uint32_t heartbeat;

}AIRPLANE_STATUS;


/*
 *******************************************************************************
 * Global variables
 *******************************************************************************
 */

/* Airplane configuration */
static AIRPLANE_CONFIG Airplane_Config =
{
    .config_ID = AIRPLANE_CONFIG_ID,                        /* "1_AP" */

    .config_date = AIRPLANE_FW_DATE,                        /* 2018/03/03 */

    /* default airplane control setting */
    .model_type = AIRPLANE_NORMAL,                          /* Normal airplane */

    .is_imu_calibrated = false,
    .accel_bias = {0, 0, 0},
    .gyro_bias = {0, 0, 0},

    /* default RC channel output value, give false or true for changing direction */
    .rc_in_is_reversed =
    {
        [RCIN_THRO_IDX] = false,
        [RCIN_AILE_IDX] = false,
        [RCIN_ELEV_IDX] = false,
        [RCIN_RUDD_IDX] = false,
        [RCIN_AUX1_IDX] = false,
    },

    /* default neutral point of each RCIN channel */
    .rc_in_neutral_ticks =
    {
        [RCIN_THRO_IDX] = TIMER1_MICROS_TO_TICKS(1500),     /* 1.5 ms by default */
        [RCIN_AILE_IDX] = TIMER1_MICROS_TO_TICKS(1500),     /* 1.5 ms by default */
        [RCIN_ELEV_IDX] = TIMER1_MICROS_TO_TICKS(1500),     /* 1.5 ms by default */
        [RCIN_RUDD_IDX] = TIMER1_MICROS_TO_TICKS(1500),     /* 1.5 ms by default */
        [RCIN_AUX1_IDX] = TIMER1_MICROS_TO_TICKS(1500),     /* 1.5 ms by default */
    },

    /* default maximum pulse ticks of each RCIN channel */
    .rc_in_max_ticks =
    {
        [RCIN_THRO_IDX] = TIMER1_MICROS_TO_TICKS(2000),     /* 2.0 ms by default */
        [RCIN_AILE_IDX] = TIMER1_MICROS_TO_TICKS(2000),     /* 2.0 ms by default */
        [RCIN_ELEV_IDX] = TIMER1_MICROS_TO_TICKS(2000),     /* 2.0 ms by default */
        [RCIN_RUDD_IDX] = TIMER1_MICROS_TO_TICKS(2000),     /* 2.0 ms by default */
        [RCIN_AUX1_IDX] = TIMER1_MICROS_TO_TICKS(2000),     /* 2.0 ms by default */
    },

    /* default minimum pulse ticks of each RCIN channel */
    .rc_in_min_ticks =
    {
        [RCIN_THRO_IDX] = TIMER1_MICROS_TO_TICKS(1000),     /* 1.0 ms by default */
        [RCIN_AILE_IDX] = TIMER1_MICROS_TO_TICKS(1000),     /* 1.0 ms by default */
        [RCIN_ELEV_IDX] = TIMER1_MICROS_TO_TICKS(1000),     /* 1.0 ms by default */
        [RCIN_RUDD_IDX] = TIMER1_MICROS_TO_TICKS(1000),     /* 1.0 ms by default */
        [RCIN_AUX1_IDX] = TIMER1_MICROS_TO_TICKS(1000),     /* 1.0 ms by default */
    },

    /* default failsafe control pulse of each RCIN channel */
    .rc_in_failsafe_ticks =
    {
        [RCIN_THRO_IDX] = TIMER1_MICROS_TO_TICKS(1000),     /* Shutdown engine */
        [RCIN_AILE_IDX] = TIMER1_MICROS_TO_TICKS(1500),     /* Set to neutral */
        [RCIN_ELEV_IDX] = TIMER1_MICROS_TO_TICKS(1500),     /* Set to neutral */
        [RCIN_RUDD_IDX] = TIMER1_MICROS_TO_TICKS(1500),     /* Set to neutral */
        [RCIN_AUX1_IDX] = TIMER1_MICROS_TO_TICKS(2000),     /* Return to home */
    },

    /* default roll PID tuning setting */
    .pid_aile_cfg =
    {
        .KP = 21.00,                                        /* KP */
        .KI = 7.14,                                         /* KI */
        .KD = 0.76,                                         /* KD */
        .scale = 1.0,                                       /* PID scale */
        .integral_max = 5.0,                                /* +- 5 degree */
        .output_max = TIMER1_MICROS_TO_TICKS(500),          /* +- 500 us */
    },

    /* default pitch PID tuning setting */
    .pid_elev_cfg =
    {
        .KP = 23.80,                                        /* KP */
        .KI = 10.23,                                        /* KI */
        .KD = 0.46,                                         /* KD */
        .scale = 1.0,                                       /* PID scale */
        .integral_max = 5.0,                                /* +- 5 degree */
        .output_max = TIMER1_MICROS_TO_TICKS(500),          /* +- 500 us */
    },

    /* default yaw PID tuning setting */
    .pid_rudd_cfg =
    {
        .KP = 14.0,                                         /* KP */
        .KI = 3.80,                                         /* KI */
        .KD = 0.5,                                          /* KD */
        .scale = 1.0,                                       /* PID scale */
        .integral_max = 5.0,                                /* +- 5 degree */
        .output_max = TIMER1_MICROS_TO_TICKS(500),          /* +- 500 us */
    },

    /* default bank turn (yaw to roll) PID tuning setting */
    .pid_bank_turn_cfg =
    {
        .KP = 0.8,                                          /* KP */
        .KI = 0.5,                                          /* KI */
        .KD = 0.005,                                        /* KD */
        .scale = 1.0,                                       /* PID scale */
        .integral_max = 5.0,                                /* +- 0 degree */
        .output_max = 30.0,                                 /* +- 30 degree */
    },

    .navigation =
    {
        .loiter_radius = 0.0,

        .current_wpt_idx = 0,
        .total_wpt = 0,
        .wpt = {
            [0] = {false, {0.0, 0.0}},
            [1] = {false, {0.0, 0.0}},
            [2] = {false, {0.0, 0.0}},
            [3] = {false, {0.0, 0.0}},
            [4] = {false, {0.0, 0.0}},
        },
    },

    .rom_crc16 = 0xFFFF,
};

/* Airplane runtime status */
static AIRPLANE_STATUS Airplane_Status =
{
    /* AHRS computation, will be initialized later */
    .ahrs_data = {0},

    /* PID computation, will be initialized later */
    .pid_aile_servo = {0},
    .pid_elev_servo = {0},
    .pid_rudd_servo = {0},
    .pid_band_turn = {0},

    .setpoint =
    {
        .roll_angle = 0.0,
        .pitch_angle = 0.0,
        .heading_angle = 0.0,
    },

    /* default RC channel input value */
    .rc_pulse_in =
    {
        [RCIN_THRO_IDX] = TIMER1_MICROS_TO_TICKS(0),
        [RCIN_AILE_IDX] = TIMER1_MICROS_TO_TICKS(0),
        [RCIN_ELEV_IDX] = TIMER1_MICROS_TO_TICKS(0),
        [RCIN_RUDD_IDX] = TIMER1_MICROS_TO_TICKS(0),
        [RCIN_AUX1_IDX] = TIMER1_MICROS_TO_TICKS(0)
    },

    /* default RC channel output value */
    .rc_pulse_out =
    {
        [RCIN_THRO_IDX] = TIMER1_MICROS_TO_TICKS(1000),
        [RCIN_AILE_IDX] = TIMER1_MICROS_TO_TICKS(1500),
        [RCIN_ELEV_IDX] = TIMER1_MICROS_TO_TICKS(1500),
        [RCIN_RUDD_IDX] = TIMER1_MICROS_TO_TICKS(1500),
    },

    .general =
    {
        .fly_mode = AIRPLANE_MANUAL_FLY,                    /* Manual fly by default */

        .imu_fail_cnt = 0,
        .ahrs_delay_cnt = 0,
        .rcin_cyc_cnt = 0,
        .rcout_cyc_cnt = 0,
        .delta_ctrl_time = 0,

        .mcu_vcc = 0.0,
    },

    .current_cruise_state = AIRPLANE_CRUISE_AWAYFROM_WPT,

    .heartbeat = 0,
};

/* GPS and navigation status */
static GPS_DATA Airplane_GPS;

#if AIRPLANE_STATUS_SNAPSHOT_EN
static AIRPLANE_STATUS Airplane_StatusSnapshot = {0};
#endif


/*
 *******************************************************************************
 * Public functions declaration
 *******************************************************************************
 */


/*
 *******************************************************************************
 * Private functions declaration
 *******************************************************************************
 */

static int8_t Airplane_Init();
static void Airplane_FlyCtrl();
static int8_t Airplane_LoadConfig(AIRPLANE_CONFIG *p_config);
static int8_t Airplane_SaveConfig(AIRPLANE_CONFIG *p_config);
static int8_t Airplane_ClearConfig(AIRPLANE_CONFIG *p_config);
static void Airplane_RemoteCtrlCalibration();
static void Airplane_ConfigControl();
static uint8_t Airplane_GetDipSwOpt();
static void Airplane_UpdateAdcIO();
static int8_t Airplane_MixRC(int16_t *p_aile_mix_diff, int16_t *p_elev_mix_diff,
                             int16_t *p_rudd_mix_diff, AIRPLANE_TYPE wing_type);
static void Airplane_UpdatePidParam();
static AIRPLANE_FLY_MODE Airplane_ChkFlyMode(uint16_t *p_rc_in);
static float Airplane_CalAngleDiff(float current_angle, float target_angle,
                                   float max_angle, float min_angle);
static void Airplane_TxMessage(uint32_t delta_time);
static void Airplane_RxMessage();


/*
 *******************************************************************************
 * Public functions
 *******************************************************************************
 */

/**
 * setup - Initializing function of Arduino.
 *
 * @param   [none]
 * @return  [none]
 *
 */
void setup()
{
    Airplane_Init();
}

/**
 * loop - Arduino main loop function.
 *
 * @param   [none]
 * @return  [none]
 *
 */
void loop()
{
    Airplane_FlyCtrl();

    /* Blink twice per second for AIRPLANE_RETURN_TO_HOME mode. */
    if(Airplane_Status.general.fly_mode == AIRPLANE_RETURN_TO_HOME){
        LEDS_Lightning(LEDS_MASTER_IDX, 600, 100, 100);
    }
    /* Blink twice per 2 second for AIRPLANE_SELF_STABILIZE mode. */
    else if(Airplane_Status.general.fly_mode == AIRPLANE_SELF_STABILIZE){
        LEDS_Lightning(LEDS_MASTER_IDX, 1600, 100, 100);
    }
    /* Blink twice per 4 second for manual mode. */
    else{
        LEDS_Lightning(LEDS_MASTER_IDX, 3600, 100, 100);
    }
}


/*
 *******************************************************************************
 * Private functions
 *******************************************************************************
 */

/**
 * Airplane_Init - Function to initialize airplane flight controller.
 *
 * @param   [none]
 *
 * @return  [int8_t]    Function executing result.
 * @retval  [0]         Success.
 * @retval  [-1]        Fail.
 *
 */
static int8_t Airplane_Init()
{
    const char *p_ret_msg[] = {"OK", "Fail"};
    int8_t imu_error = 0;
    int8_t rom_error = 0;
    IMU_SENSOR_DATA imu_sensor_data = {0};
    uint8_t total_wpt;
    uint8_t current_wpt_idx;

    /* UART0 initialization */
    Uart0_Init(57600);
    Uart0_Println(PSTR("[Airplane] ONERC_LIB"));
    Uart0_Println(PSTR("[Airplane] FW date = %X"), AIRPLANE_FW_DATE);

    /* LEDs initialization */
    LEDS_Init();

    /* Timers initialization */
    Timers_Init();

    /* ADC pins initialization */
    ADC_Init();

    /* I2C initialization */
    I2C_Init(400000);

    /* Pin change function initialization */
    PC_Init();

#if UARTS_FUNCTION_EN
    /* Simulated UART initialization */
    UartS_Init(9600);
#endif

	/* MCU protocol initialization */
    MP_Init();

    /* Load airplane configuration from EEPROM */
    Uart0_Printf(PSTR("[ROM] Load: "));
    rom_error = Airplane_LoadConfig(&Airplane_Config);
    Uart0_Println(PSTR("%s (0x%hX)"),
                  rom_error ? p_ret_msg[1] : p_ret_msg[0],
                  Airplane_Config.rom_crc16);
    Uart0_Println(PSTR("[ROM] ID = %X, date = %X"),
                  Airplane_Config.config_ID,
                  Airplane_Config.config_date);

    /* Initial RC input channel */
    RCIN_SetNeutral(Airplane_Config.rc_in_neutral_ticks);
    RCIN_SetFailsafe(Airplane_Config.rc_in_failsafe_ticks);
    RCIN_SetDirection(Airplane_Config.rc_in_is_reversed);
    RCIN_SetMaxMinStick(Airplane_Config.rc_in_max_ticks, Airplane_Config.rc_in_min_ticks);
    RCIN_Init();

    /* Initial RC output channel */
    RCOUT_Init();

    /* Initial fail safe function */
    FailSafe_Init();

    /* Initial GPS hardware module and functions */
    GPS_Init(&Airplane_GPS);

    /* Setup first waypoint if it's activated */
    total_wpt = Airplane_Config.navigation.total_wpt;
    current_wpt_idx = Airplane_Config.navigation.current_wpt_idx;
    if(total_wpt > 0 && Airplane_Config.navigation.wpt[current_wpt_idx].is_actived == true){

        LEDS_PwrON(LEDS_MASTER_IDX);
        LEDS_PwrON(LEDS_SLAVE_IDX);
        Timer1_DelayMillis(500);
        LEDS_PwrOFF(LEDS_MASTER_IDX);
        LEDS_PwrOFF(LEDS_SLAVE_IDX);

        GPS_SetWpt(&Airplane_GPS, &Airplane_Config.navigation.wpt[current_wpt_idx].wpt_coord);

        Uart0_Printf(PSTR("[GPS] home: "));
        Uart0_Printf(PSTR("LAT_DD = "));
        Uart0_PrintFloat(Airplane_Config.navigation.wpt[current_wpt_idx].wpt_coord.LAT_DD, 4);
        Uart0_Printf(PSTR(", LONG_DD = "));
        Uart0_PrintFloat(Airplane_Config.navigation.wpt[current_wpt_idx].wpt_coord.LONG_DD, 4);
        Uart0_Println(PSTR(""));
    }

    Uart0_Println(PSTR("[GPS] loiter radius = %f meters"), AIRPLANE_GET_LOITER_RADIUS());

    /* Initial IMU sensors */
    LEDS_PwrON(LEDS_SLAVE_IDX);

    imu_error = IMU_Init();
    if(imu_error != 0){
        while(1);
    }
    else{
        /* Apply IMU bias setting directly if the ROM data is available */
        if(Airplane_Config.is_imu_calibrated == true)
            IMU_SetCalibratedBias(Airplane_Config.accel_bias, Airplane_Config.gyro_bias);
        /* Otherwise, perform calibration procedure */
        else
            IMU_DoCalibration(IMU_SENSOR_CAL_MODE);

        Uart0_Println(PSTR("[IMU] Accel Bias XYZ: %hd, %hd, %hd"),
                      Airplane_Config.accel_bias[0],
                      Airplane_Config.accel_bias[1],
                      Airplane_Config.accel_bias[2]);

        Uart0_Println(PSTR("[IMU] Gyro Bias XYZ: %hd, %hd, %hd"),
                      Airplane_Config.gyro_bias[0],
                      Airplane_Config.gyro_bias[1],
                      Airplane_Config.gyro_bias[2]);
    }

    LEDS_PwrOFF(LEDS_SLAVE_IDX);

    /* Initial AHRS function */
    IMU_Get6RawData(&imu_sensor_data);
    AHRS_Init(&(Airplane_Status.ahrs_data), imu_sensor_data.accel_raw);

    /* Initial PID data and parameters for ROLL */
    PID_Create(&Airplane_Status.pid_aile_servo);
    PID_SetTuning(&Airplane_Status.pid_aile_servo,
                  Airplane_Config.pid_aile_cfg.KP,
                  Airplane_Config.pid_aile_cfg.KI,
                  Airplane_Config.pid_aile_cfg.KD);
    PID_SetScaleFactor(&Airplane_Status.pid_aile_servo, Airplane_Config.pid_aile_cfg.scale);
    PID_SetIntegralMax(&Airplane_Status.pid_aile_servo, Airplane_Config.pid_aile_cfg.integral_max);
    PID_SetOutputMax(&Airplane_Status.pid_aile_servo, Airplane_Config.pid_aile_cfg.output_max);

    /* Initial PID data and parameters for PITCH */
    PID_Create(&Airplane_Status.pid_elev_servo);
    PID_SetTuning(&Airplane_Status.pid_elev_servo,
                  Airplane_Config.pid_elev_cfg.KP,
                  Airplane_Config.pid_elev_cfg.KI,
                  Airplane_Config.pid_elev_cfg.KD);
    PID_SetScaleFactor(&Airplane_Status.pid_elev_servo, Airplane_Config.pid_elev_cfg.scale);
    PID_SetIntegralMax(&Airplane_Status.pid_elev_servo, Airplane_Config.pid_elev_cfg.integral_max);
    PID_SetOutputMax(&Airplane_Status.pid_elev_servo, Airplane_Config.pid_elev_cfg.output_max);

    /* Initial PID data and parameters for YAW */
    PID_Create(&Airplane_Status.pid_rudd_servo);
    PID_SetTuning(&Airplane_Status.pid_rudd_servo,
                  Airplane_Config.pid_rudd_cfg.KP,
                  Airplane_Config.pid_rudd_cfg.KI,
                  Airplane_Config.pid_rudd_cfg.KD);
    PID_SetScaleFactor(&Airplane_Status.pid_rudd_servo, Airplane_Config.pid_rudd_cfg.scale);
    PID_SetIntegralMax(&Airplane_Status.pid_rudd_servo, Airplane_Config.pid_rudd_cfg.integral_max);
    PID_SetOutputMax(&Airplane_Status.pid_rudd_servo, Airplane_Config.pid_rudd_cfg.output_max);

    /* Initial PID data and parameters for bank turn */
    PID_Create(&Airplane_Status.pid_band_turn);
    PID_SetTuning(&Airplane_Status.pid_band_turn,
                  Airplane_Config.pid_bank_turn_cfg.KP,
                  Airplane_Config.pid_bank_turn_cfg.KI,
                  Airplane_Config.pid_bank_turn_cfg.KD);
    PID_SetScaleFactor(&Airplane_Status.pid_band_turn, Airplane_Config.pid_bank_turn_cfg.scale);
    PID_SetIntegralMax(&Airplane_Status.pid_band_turn, Airplane_Config.pid_bank_turn_cfg.integral_max);
    PID_SetOutputMax(&Airplane_Status.pid_band_turn, Airplane_Config.pid_bank_turn_cfg.output_max);

    Airplane_RemoteCtrlCalibration();

    /* Launch related initializing procedure and store new configuration to ROM if needed */
    Airplane_ConfigControl();

    return 0;
}
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

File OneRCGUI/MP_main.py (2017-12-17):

import wx 
import MP_GUI
import threading
import Queue
import time
import os
import serial.tools.list_ports
import datetime
from MP_handler import MP_handler
from MP_plot import *
from MP_frames import *


class MainGUI(MP_GUI.frm_MPMain): 

    __mp_handler = MP_handler()
    __mp_att_roll_plot = None
    __mp_att_pitch_plot = None
    
    __mp_frame_queue = Queue.Queue(0)
    __mp_console_message_queue = Queue.Queue(0)
    __mp_is_console_auto_scroll = True
    __mp_is_save_log = False
    __mp_log_filename = ''
    __mp_log_file_ptr = None
    __mp_log_wbytes = 0
    
    __mp_rcin_ch0 = int(0)
    __mp_rcin_ch1 = int(0)
    __mp_rcin_ch2 = int(0)
    __mp_rcin_ch3 = int(0)
    __mp_rcin_ch4 = int(0)

    def __init__(self, parent): 
        MP_GUI.frm_MPMain.__init__(self, parent)  

        # Get com port list 
        ports = []
        for n, (port, desc, hwid) in enumerate(sorted(serial.tools.list_ports.comports()), 1):
            ports.append(port)
        
        self.combo_SerialPort.SetItems(ports)
        self.combo_SerialPort.SetSelection(0) 
        
        # Initial baud rate options
        baud = ['600', '1200', '2400', '4800', '9600', '14400', '19200', '28800',       \
                '38400', '56000', '57600', '115200', '128000', '256000']
        self.combo_BaudRate.SetItems(baud)
        self.combo_BaudRate.SetStringSelection('57600')
        
        self.text_ConsoleSavePath.AppendText(os.getcwd())
        self.text_ConsoleLines.AppendText('0')
        self.text_LogBytes.AppendText('0')
        
        self.__mp_att_roll_plot = MP_Plot(self.panel_RollAnglePlot, 'Roll angle')
        self.__mp_att_pitch_plot = MP_Plot(self.panel_PitchAnglePlot, 'Pitch angle')

        self.__mp_accel_sensor_x = MP_Plot(self.panel_AccelSensorXPlot, 'Accel Sensor X', True, 'b')
        self.__mp_accel_sensor_y = MP_Plot(self.panel_AccelSensorYPlot, 'Accel Sensor Y', True, 'b')
        self.__mp_accel_sensor_z = MP_Plot(self.panel_AccelSensorZPlot, 'Accel Sensor Z', True, 'b')
        self.__mp_gyro_sensor_x = MP_Plot(self.panel_GyroSensorXPlot, 'Gyro Sensor X', True, 'b')
        self.__mp_gyro_sensor_y = MP_Plot(self.panel_GyroSensorYPlot, 'Gyro Sensor Y', True, 'b')
        self.__mp_gyro_sensor_z = MP_Plot(self.panel_GyroSensorZPlot, 'Gyro Sensor Z', True, 'b')
        
        self.__mp_accel_vector_x = MP_Plot(self.panel_AccelVctrXPlot, 'Accel Vector X', True)
        self.__mp_accel_vector_y = MP_Plot(self.panel_AccelVctrYPlot, 'Accel Vector Y', True)
        self.__mp_accel_vector_z = MP_Plot(self.panel_AccelVctrZPlot, 'Accel Vector Z', True)
        self.__mp_gyro_vector_x = MP_Plot(self.panel_GyroVctrXPlot, 'Gyro Vector X', True)
        self.__mp_gyro_vector_y = MP_Plot(self.panel_GyroVctrYPlot, 'Gyro Vector Y', True)
        self.__mp_gyro_vector_z = MP_Plot(self.panel_GyroVctrZPlot, 'Gyro Vector Z', True)

        self.__mp_handler.set_rx_frame_queue(self.__mp_frame_queue)
        self.__thread_start()
        
    def __frame_displayer(self):

        while(True):
            item_cnt = self.__mp_frame_queue.qsize()
            cli_message = ''
            
            while(item_cnt):
                rx_data = self.__mp_frame_queue.get(True, None)
                
                self.__update_input_stick_slider(rx_data["data"])
                
                self.__frame_plotter(rx_data["data"])

                attrs = vars(rx_data["data"])
                del attrs["s_f"]
                del attrs["len"]
                del attrs["CRC16"]
                
                cli_message += rx_data["rx_time"] + ": "
                cli_message += ', '.join("%s: %s" % item for item in attrs.items())
                cli_message += '\n'

                item_cnt -= 1
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

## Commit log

2017-12-17 [OneRCFW]
    1. Import v0.1.0.
    - Auto level function.
    - Maintaining heading angle based on gyroscope.
    - FC configuration save/clean/load functions.
    - Return to home according to GPS navigation information (unstable, need to do more test).
    - RCIN calibration functions:
    * Maximum and minimum RCIN pulse width calibration.
    * Natural position calibration.
    * Failsafe configuration.
    - Corresponding schematic v1.8.
    [OneRCSchematic_v1_8.GBL, OneRCSchematic_v1_8.GBO, OneRCSchematic_v1_8.GBS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]
2018-09-01 [OneRCFW]
    1. Committed latest modification:
    - Modified MPU6050 FIFO sampling rate to 1000 Hz by default.
    - Modified Airplane_FlyCtrl function, increase the pitch setpoint (angle of attack) when the FC performing bank turn for "returning to home".
    * I did the field trial, but the airplane still lost altitude quickly while it performing the bank turn (return to home mode).
    * Although I already limit the maximum bank turn angle to +-30 degree in code, but the airplane still rolls more than 30 degree while it performing the bank turn (return to home mode).
    - Most of functions in this firmware are quite stable EXCEPT the return to home function.
2019-06-02 Update README.md
    Correct board type setting description.

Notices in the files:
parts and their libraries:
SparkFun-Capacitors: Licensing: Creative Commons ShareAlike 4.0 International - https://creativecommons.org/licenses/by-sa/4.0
